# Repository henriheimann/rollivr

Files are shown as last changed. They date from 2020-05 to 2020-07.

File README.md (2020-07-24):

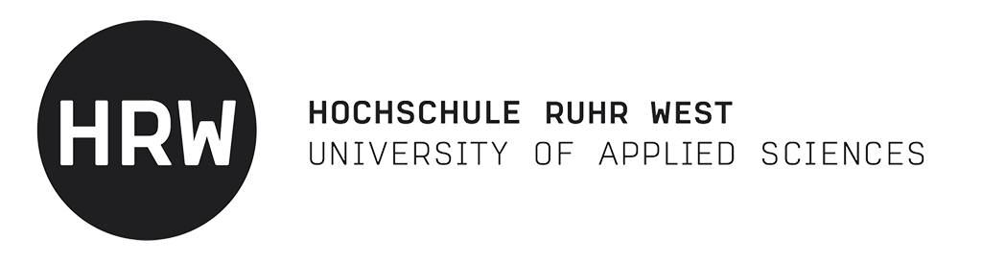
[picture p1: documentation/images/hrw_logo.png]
HRW Logo

<br/>
<br/>
<br/>

# RolliVR

This repository contains the documentation and the software and hardware components of the RolliVR project developed at [Hochschule Ruhr West](https://www.hochschule-ruhr-west.de/). RolliVR aims to create a platform for wheelchair drivers to use their wheelchair to naturally move in existing VR applications and games. For that purpose, we provide a manual along the design files for 3D-prints to create the platform and an OpenVR driver and software package to use the platform in SteamVR applications.





</br>

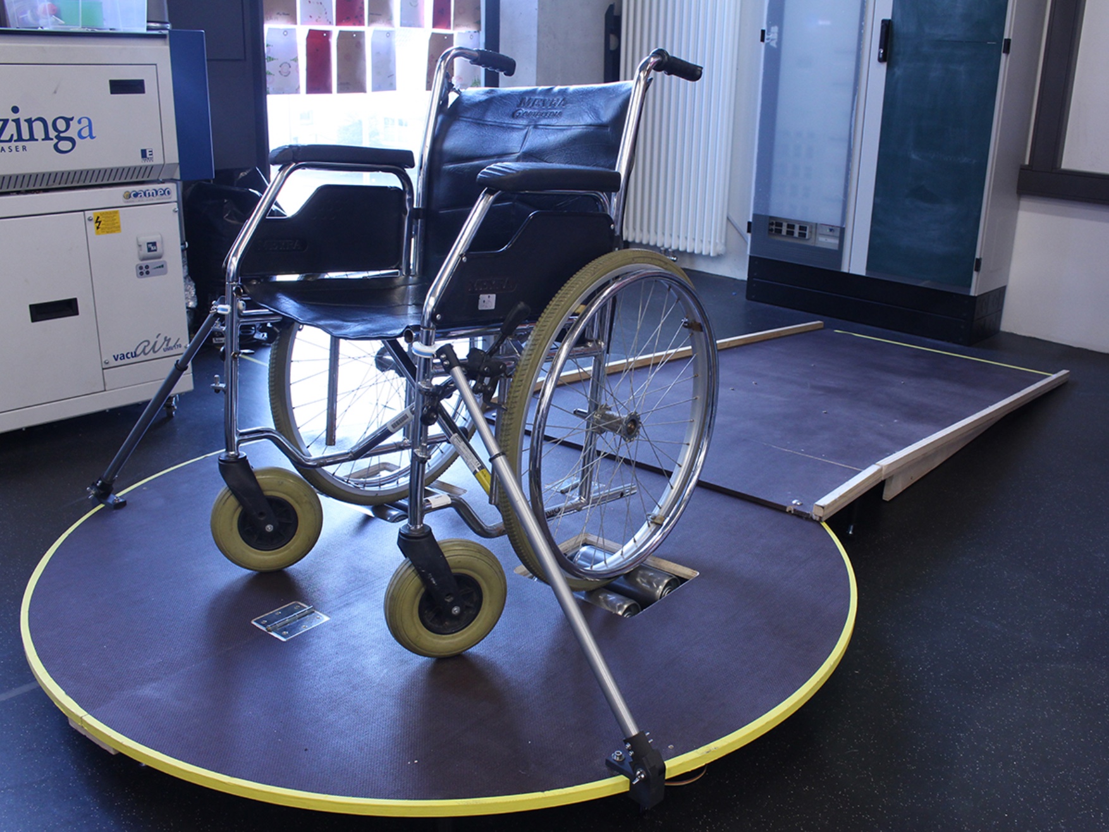
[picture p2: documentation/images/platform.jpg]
Platform


</br>
</br>

## Readme Contents

- [Building the Platform](#building-the-platform)
    - [Bill of Materials](#bill-of-materials)
    - [3D-Printed Components](#3D-Printed-Components)
    - [Electronics](#electronics)
    - [Assembly](#assembly)
- [Building the Software](#building-the-software)
    - [Required Software](#required-software)
    - [Arduino](#arduino)
    - [Driver and Overlay](#driver-and-overlay)
- [Usage Guide](#usage-guide)

## Building the Platform

### Bill of Materials

| Count | Part | Used For |
| - | - | - |
| 1 | Arduino Uno (or similar) | electronics |
| 1 | USB cable for the chosen Arduino | electronics |
| 1 | USB extension cable | electronics |
| 2 | Grove optical rotary encoder (TCUT1600X01) | electronics |
| 2 | Grove universal 4 pin cable | electronics |
| - | jumper wires | electronics |
| 2 | film coated plywood 1500x7500mm (thickness 18mm) | platform |
| 2 | hinges | platform |
| 8 | height adjustable feet (height around 10mm) | platform |
| 2 | load bearing rollers (length 200mm, diameter 80mm, 12mm thread) | platform |
| 8 | stainless steel angle brackets | platform |
| 8+ | M12 nuts | platform |
| 40+ | M5 pointed screws | platform |
| 2 | telescopic tubes (length around 1m, diameter 18mm to 22.5mm) | wheelchair bracket |
| 8+ | M3 screws (length 40mm) | wheelchair bracket |
| 8+ | M3 nuts | wheelchair bracket |
| 8+ | M3 washers | wheelchair bracket |
| 6+ | M5 screws (length 40mm) | wheelchair bracket |
| 6+ | M5 nuts | wheelchair bracket |
| 6+ | M5 washers | wheelchair bracket |
| - | flexible filament (TPU) | wheelchair bracket |
| - | dark filament | encoder disk |
| - | any filament | other 3D-printed parts |
| - | double sided tape | encoder disk |
| - | duct tape | wiring |

### 3D-Printed Components

#### Encoder Ring

The encoder ring must be printed with a dark filament to properly block the light of the rotary encoder's LEDs. ([.stl](hardware/encoder-ring/encoder-ring.stl))

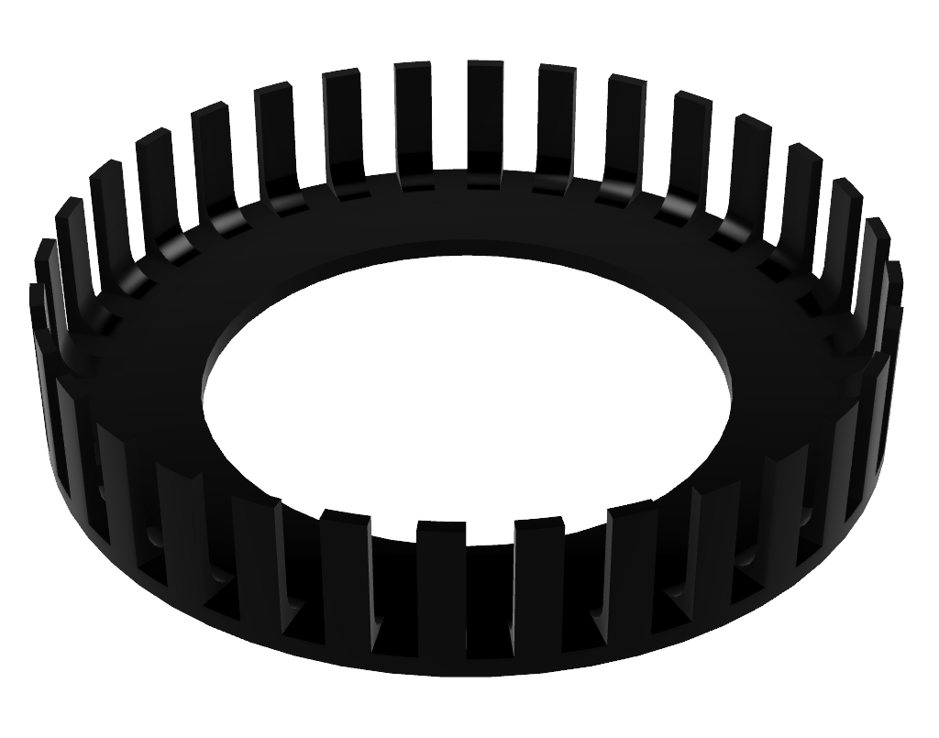
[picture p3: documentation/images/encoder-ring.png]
Encoder Ring


#### Encoder Holder

The encoder holder can be printed with a filament of your choice. ([.stl](hardware/encoder-holder/encoder-holder.stl))

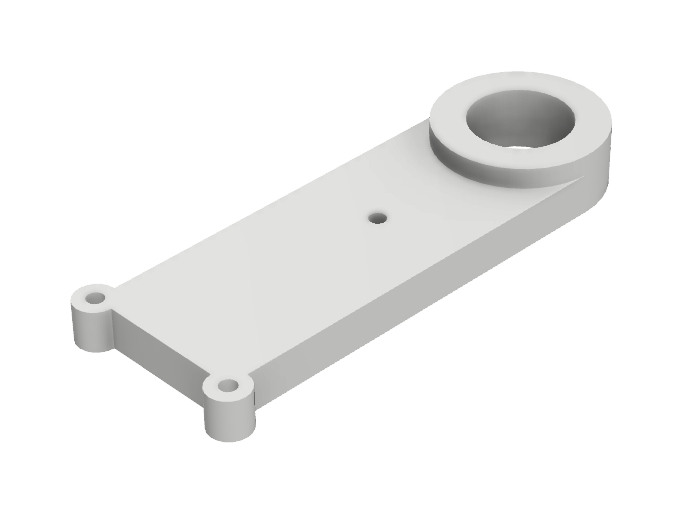
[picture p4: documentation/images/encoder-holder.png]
Encoder Holder


#### Platform Bracket

Both parts of the platform bracket can be printed with a filament of your choice. ([first .stl](hardware/platform-bracket/platform-bracket-1.stl), [second .stl](hardware/platform-bracket/platform-bracket-2.stl))

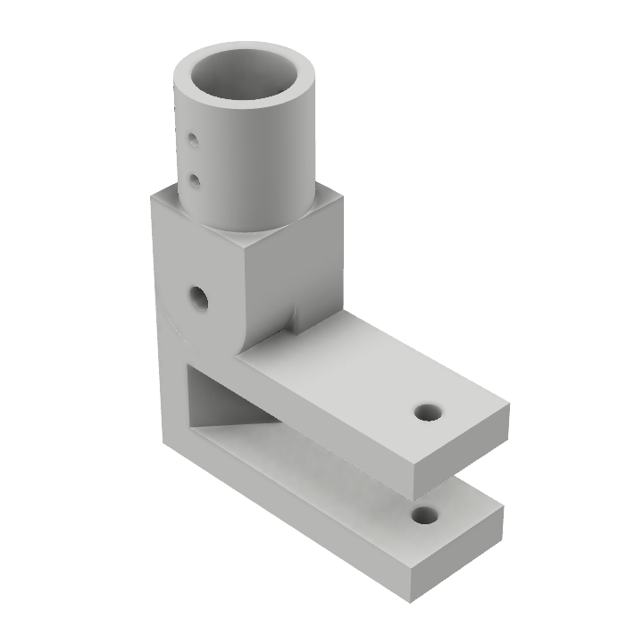
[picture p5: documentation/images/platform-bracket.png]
Platform Bracket


#### Wheelchair Bracket

Most parts of the wheelchair bracket can be printed with a filament of your choice. ([first .stl](hardware/wheelchair-bracket/wheelchair-bracket-1.stl), [second .stl](hardware/wheelchair-bracket/wheelchair-bracket-2.stl)) The part holding onto the wheelchair should be printed with flexible filament (TPU) for a better grip and to prevent any scratches. ([third .stl](hardware/wheelchair-bracket/wheelchair-bracket-3.stl)) The second and third parts (the parts holding onto the wheelchair) have to be printed twice to form the grip.  

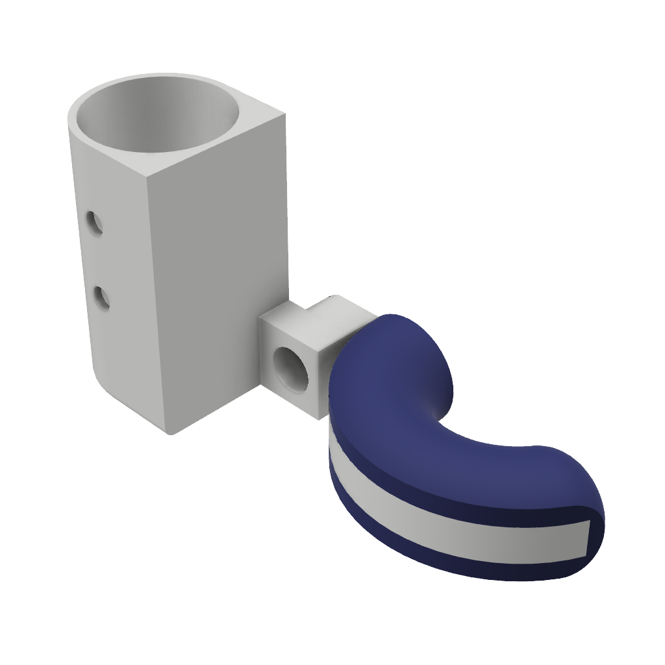
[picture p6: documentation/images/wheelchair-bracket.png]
Wheelchair Bracket
 

### Assembly

#### Platform

Firstly, cut the two film coated plywood boards into semicircles with a diameter of 750mm. Align them and use two hinges to combine the two halves into a complete circle. This allows for easier transport of the platform. Cut out two holes which will later house the load bearing rollers according to the following drawing.

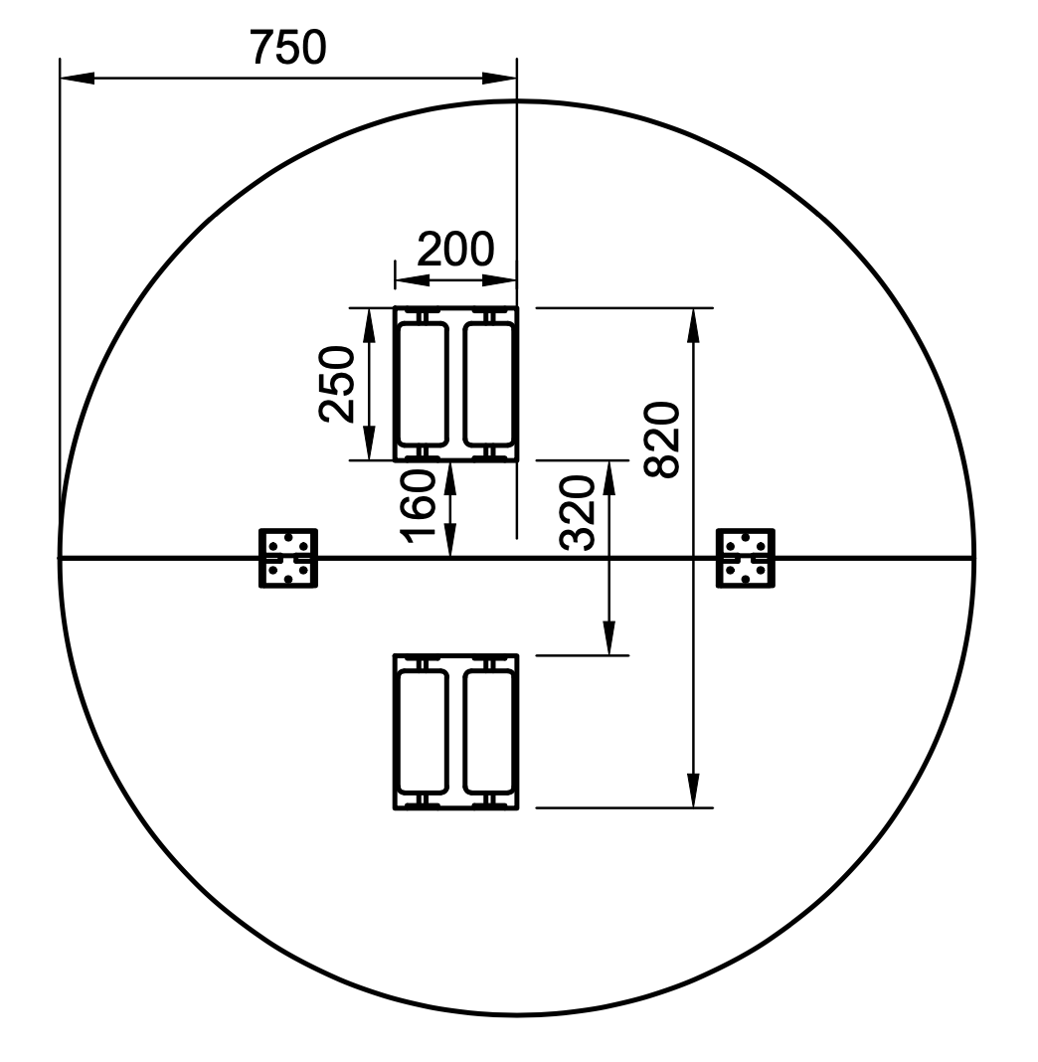
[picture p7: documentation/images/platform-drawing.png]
Platform Drawing


Evenly space out and screw the eight height adjustable feet to the bottom of the board to elevate it to a height of about 10cm.

#### Rollers

Place the 3d-printed encoder rings over two of the rollers and fixate them using double sided tape on their bottom side.

Use a single screw to fix the optical rotary encoder onto the 3d printed holder. Anchor each load bearing roller between two angle brackets putting the rotary encoder holders (where applicable) and nuts in between as seen in the image below.

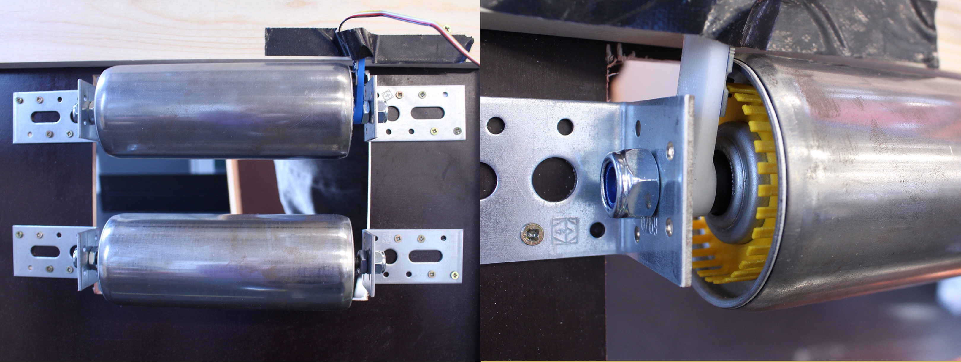
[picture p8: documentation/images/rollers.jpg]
Rollers


Screw the angle brackets to the platform afterwards.

#### Bracket

Assemble the wheelchair and platform brackets using the M5 and M3 screws, nuts and washers as seen in the image below.

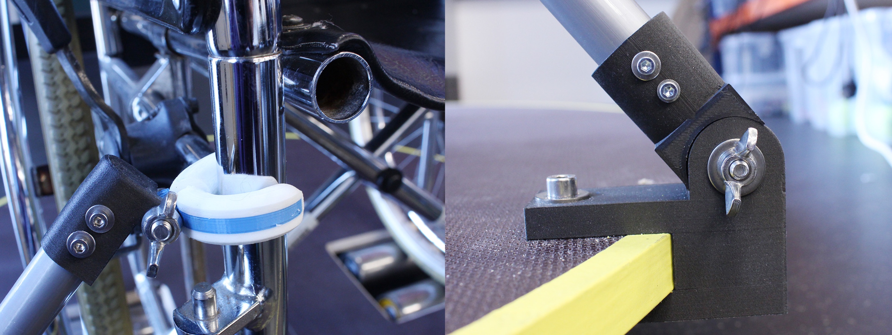
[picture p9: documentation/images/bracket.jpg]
Bracket


### Electronics

Both optical encoders need to be connected to the Arduino's VCC and ground pins and the respective digital input pins 6 to 9 as shown in the image below.

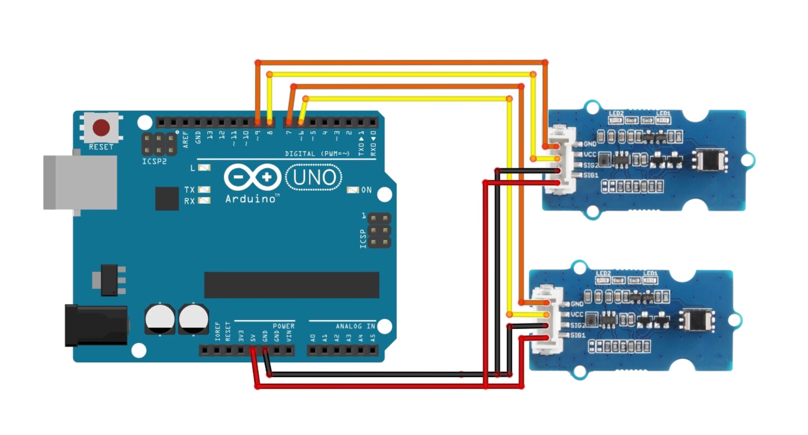
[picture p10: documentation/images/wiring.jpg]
Wiring


## Building the Software

### Required Libraries & Tools

| Software | License | Recommended Installation Method |
| - | - | - |
| Qt5 | LGPLv3 | Download and install from [here](https://www.qt.io/download-qt-installer) |
| OpenVR | BSD 3 | Install via vcpkg |
| GLM | MIT | Install via vcpkg |
| Serial | MIT | Fork integrated as submodule of this repository |
| NSIS | zlib | Download install from [here](https://nsis.sourceforge.io/Download) |
| NSIS Json Plugin | See LICENSE.txt | Included in this repository |
| CMake | New BSD | Download and install from [here](https://cmake.org/download/) |
| Arduino IDE | LGPL | Download and install from [here](https://www.arduino.cc/en/main/software) |

### Driver and Overlay

[CMake](https://cmake.org/download/) is used as build tool. OpenVR and GLM libraries need to be installed on your machine. It is recommended that you download them via [vcpkg](https://github.com/Microsoft/vcpkg). Make sure to install the x64-windows triplets to be able to build the driver and overlay as 64 bit applications:

`vcpkg install openvr glm --triplet x64-windows`

[Qt5](https://www.qt.io/download-open-source) has to be installed to build the overlay, as it is used for the user interface. To build the installer [NSIS](https://nsis.sourceforge.io/Download) has to be installed. With this prerequisites installed and the repository cloned, make sure that you that you have initialized the required submodules via the execution of the following command in the root directory:

`git submodule update --init`

In the software directory, create a build directory and move to it:

`cd software && mkdir build && cd build`

Execute CMake, make sure the TOOLCHAIN_FILE and PREFIX_PATH variables match your installation paths. Set your required release type and specify the generator:

`cmake .. -DCMAKE_BUILD_TYPE=Release -G"Visual Studio 16 2019" -DCMAKE_TOOLCHAIN_FILE=C:\vcpkg\scripts\buildsystems\vcpkg.cmake -DCMAKE_PREFIX_PATH=C:\Qt\5.14.2\msvc2017_64\lib\cmake`

Perform the build:

`cmake --build . --config Release`

After the build, the driver folder structure and files will available as `<Path to Repo>\software\build\driver\rollivr` and the overlay folder structure and files will be copied to the output folder as `<Path to Repo>\software\build\overlay\rollivr`.

If you want to create the installer execute the following command:

`cmake --build . --target package --config Release`

The installer will then be located at `<Path to Repo>\build\RolliVR-Installer.exe`.
	
Alternatively, you can access the most recent prebuild installer in the latest completed action.

### Arduino

There are two Arduino projects provided in this repository:

- [arduino-software-debug](embedded/arduino-software-debug) serves as a mean to test the software without the platform. Simply wire two pushbuttons with pullup resistors to the A0 and A5 pins of an Arduino and flash this sketch. Holding down buttons simulates a forward movement of the left and right wheels.

- [arduino-software-encoder](embedded/arduino-software-encoder) is the software required for the real platform. It transmits the movement distance and angle calculated from the values of the optical rotary encoders every 100 milliseconds. It also applies a rolling average filter over 5 samples.

## Usage Guide

After building `RolliVR-Installer.exe` launch it and install RolliVR to a directory of your choice.

### Driver

Launch SteamVR after the installation. Connect the Arduino with the firmware flashed to the PC running SteamVR and take a look at the information panel. If no icon is shown at all, make sure an entry in the `external_drivers` array in the `<User>\AppData\Local\openvr\openvrpaths.vrpath` file points to `<RolliVR Installation Directory>\driver\rollivr`. If the RolliVR icon is greyed out, the connection could not be established, if it is blue-greenish, the Arduino is successfully sending data.

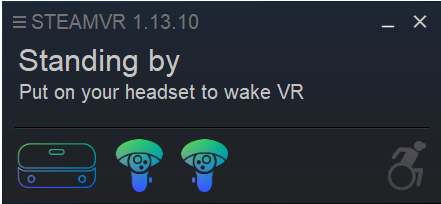
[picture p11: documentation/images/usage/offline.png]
Offline

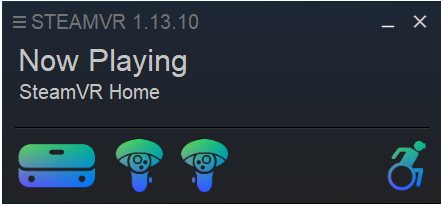
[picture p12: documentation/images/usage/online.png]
Online


In case of a failed connection go to the SteamVR developer console:

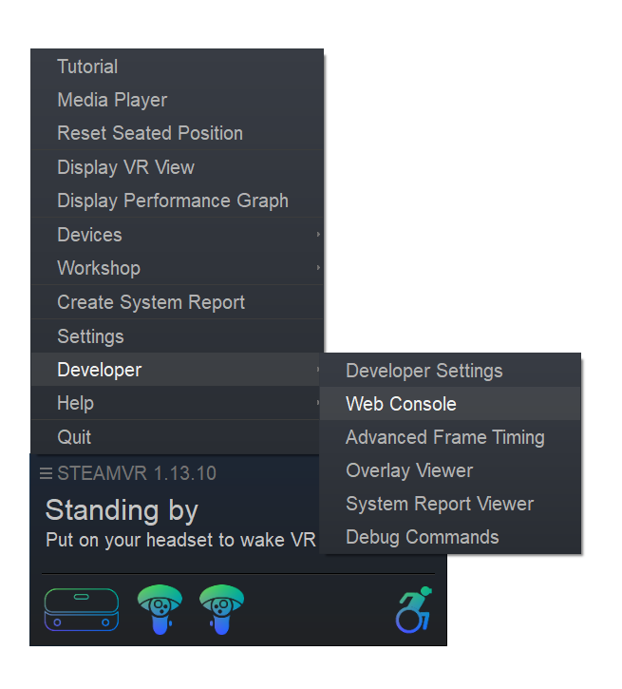
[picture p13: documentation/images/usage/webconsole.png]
Web Console


Search for RolliVR and find the logs of available and accepted hardware ids. Available hardware ids are the ids of serial ports connected to your system. Accepted hardware ids are the ids the driver expects.

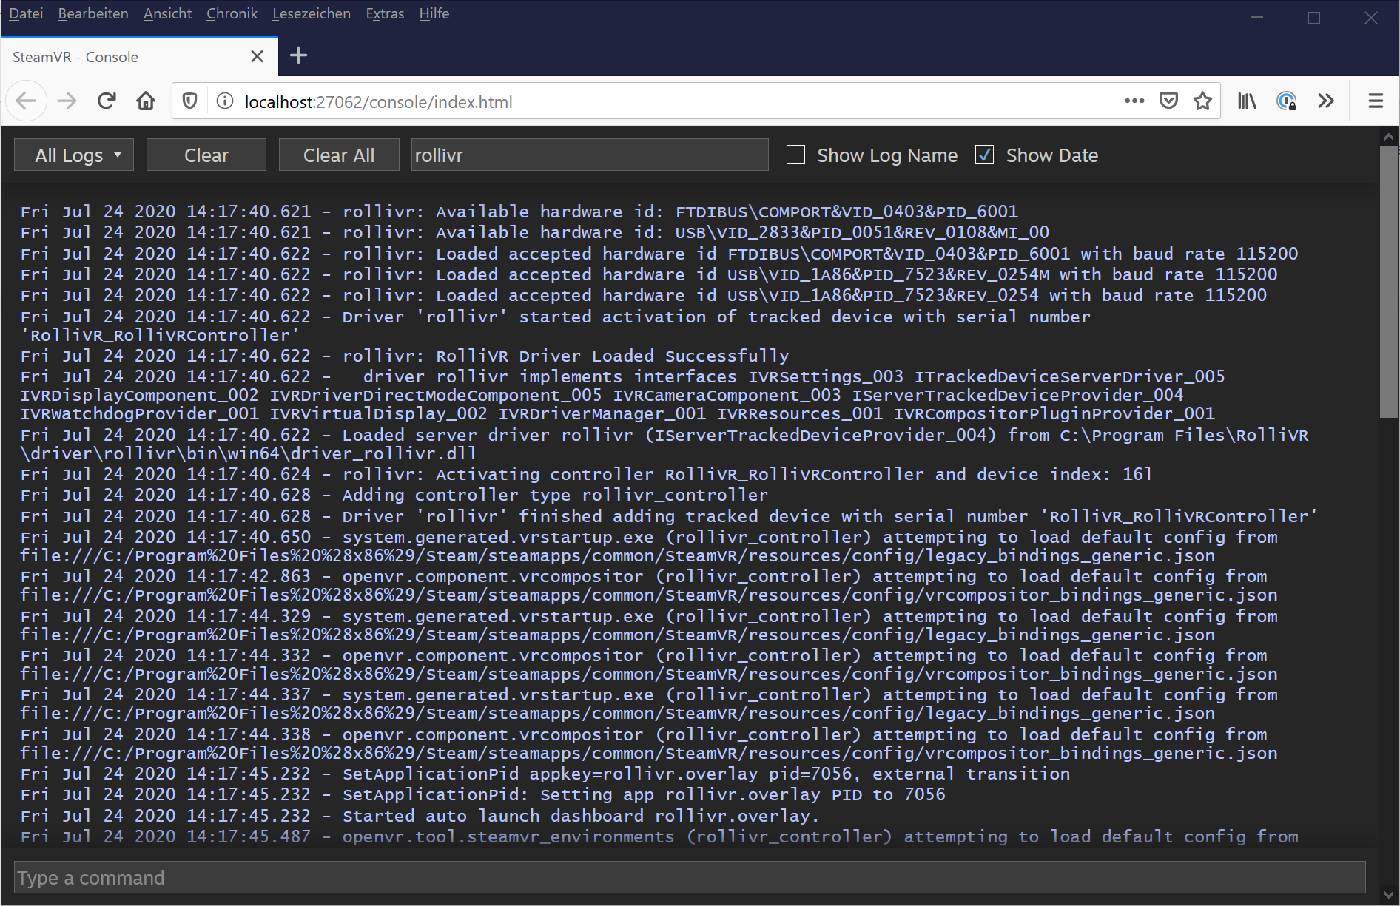
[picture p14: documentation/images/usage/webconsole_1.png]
Web Console


If your Arduino has a hardware id that is not accepted, add the hardware id and baudrate to the config file located at `<RolliVR Installation Directory>\driver\rollivr\resources\config\comports.txt`. Restart SteamVR afterwards. The Arduino should successfully connect and you can test the controller by accessing `#/USER/TREADMILL` under Controllers > Test Controller. VR Applications that allow custom controller bindings can now be configured to use the RolliVR controller as an input.

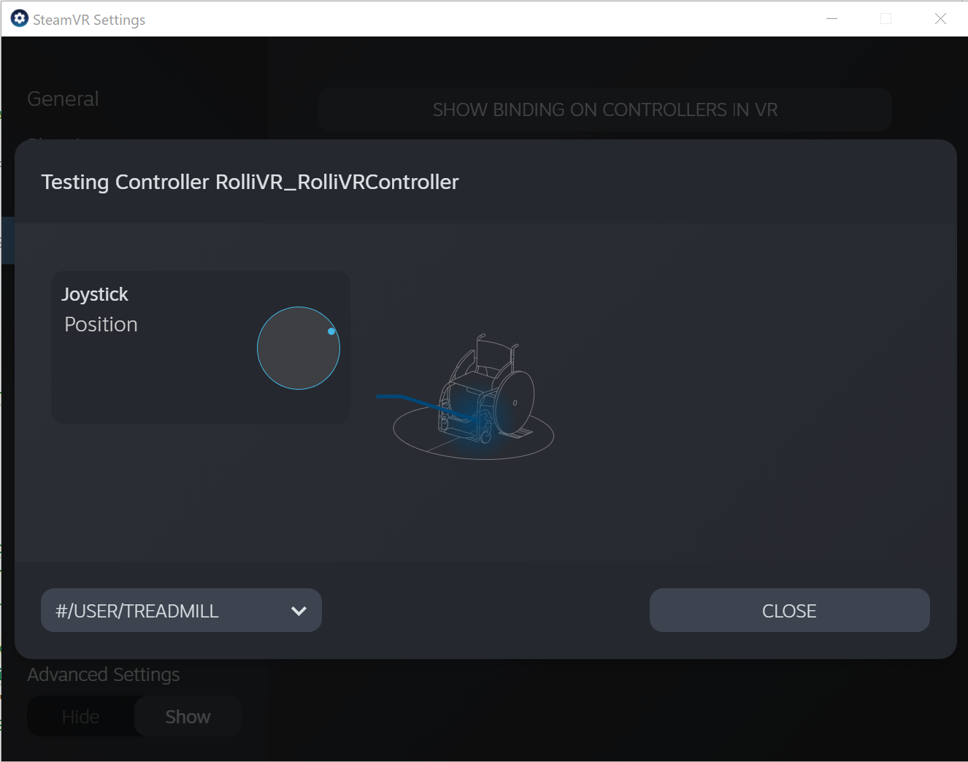
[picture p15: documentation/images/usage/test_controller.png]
Test Controller


### Overlay

When using roomscale VR applications with RolliVR, the overlay is required. To make sure the overlay has correctly registered itself as an autostart application, go to Choose Startup Overlay Apps under Startup / Shutdown. If RolliVR is displayed, you are good to continue, otherwise run `install_manifest.bat` in the installation directory and restart SteamVR. RolliVR should now be correctly registered and enabled as autostart application:

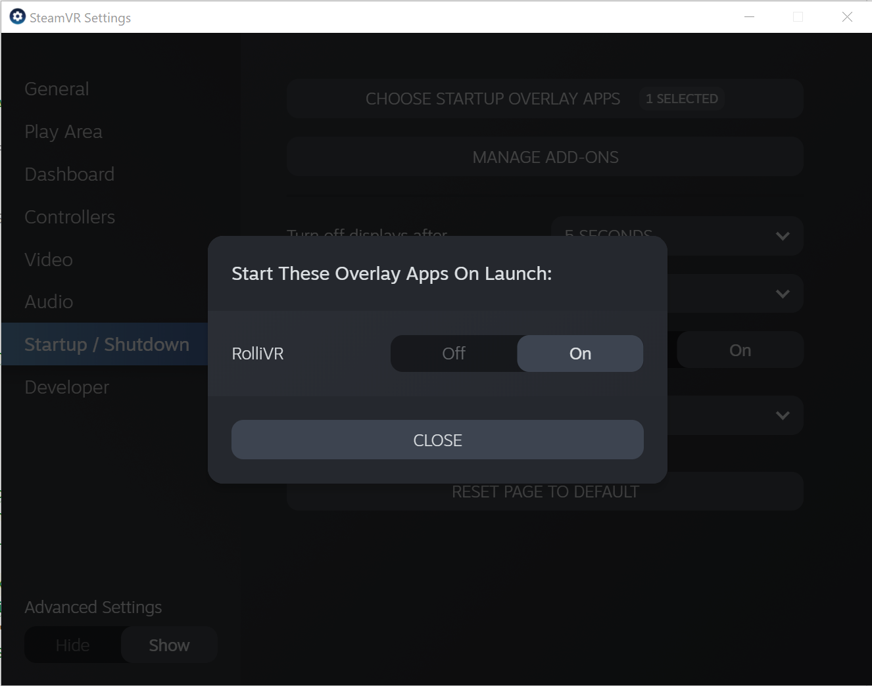
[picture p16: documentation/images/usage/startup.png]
Autostart Applications


The driver and the overlay need to be connected next. Go to the Controllers and make sure advanced settings are shown. Click on Show Old Binding UI.

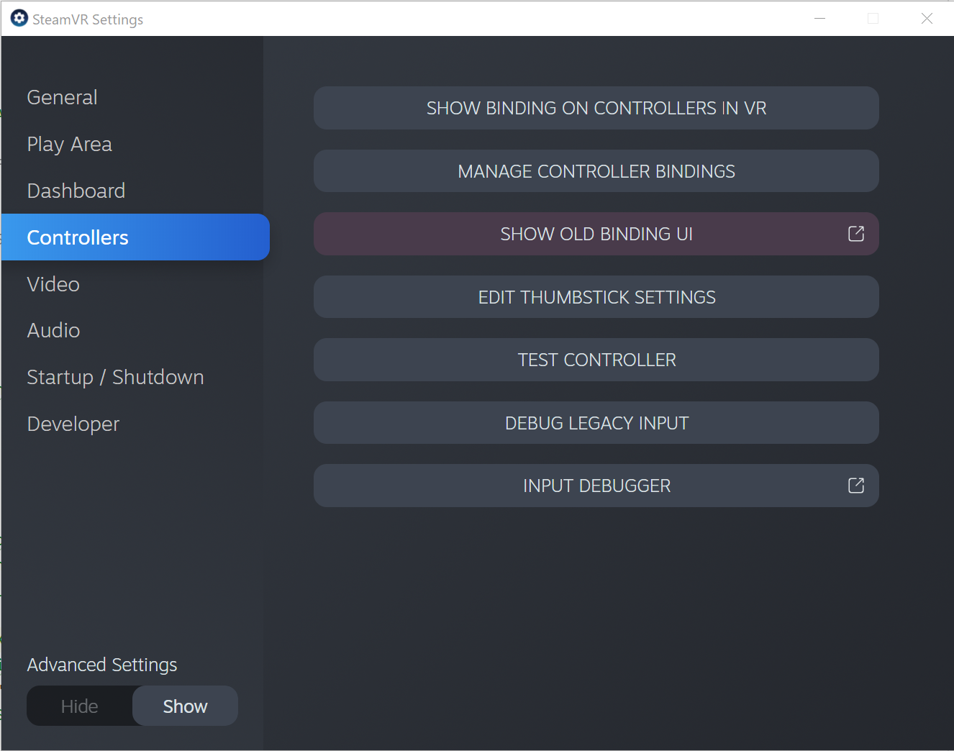
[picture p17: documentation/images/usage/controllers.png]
Controllers Menu


Now proceed to edit the bindings of RolliVR. You may need to click on Show More Applications before it shows up.

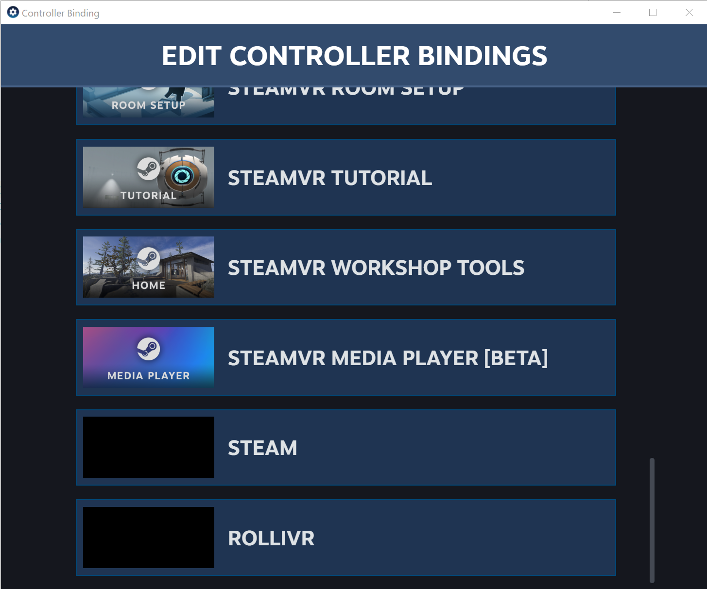
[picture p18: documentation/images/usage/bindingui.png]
Binding UI


Firstly, change the controller used for the RolliVR application. This defaults to your VR headsets controllers, but it needs to be changed to the RolliVR Controllers. To do so, click on the name of the Current Controller and select the RolliVR Controller in the following menu.

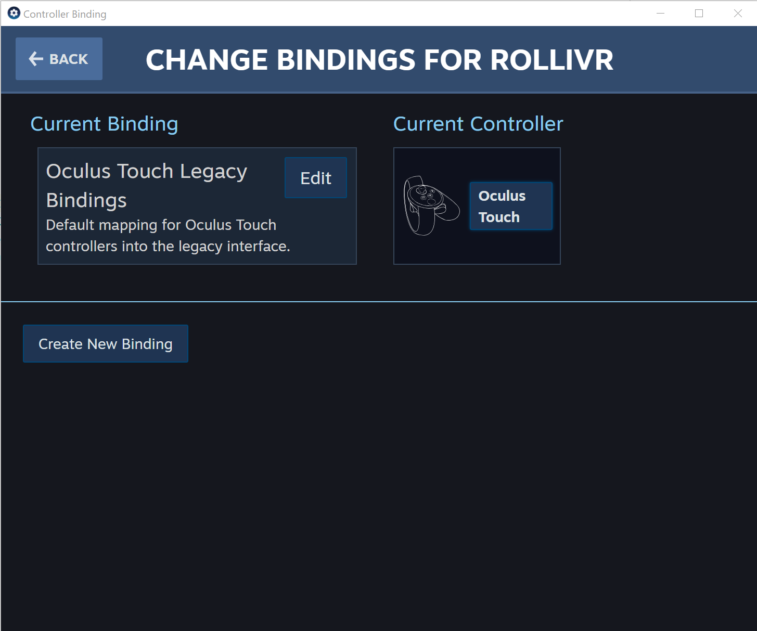
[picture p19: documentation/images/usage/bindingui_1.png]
Binding UI


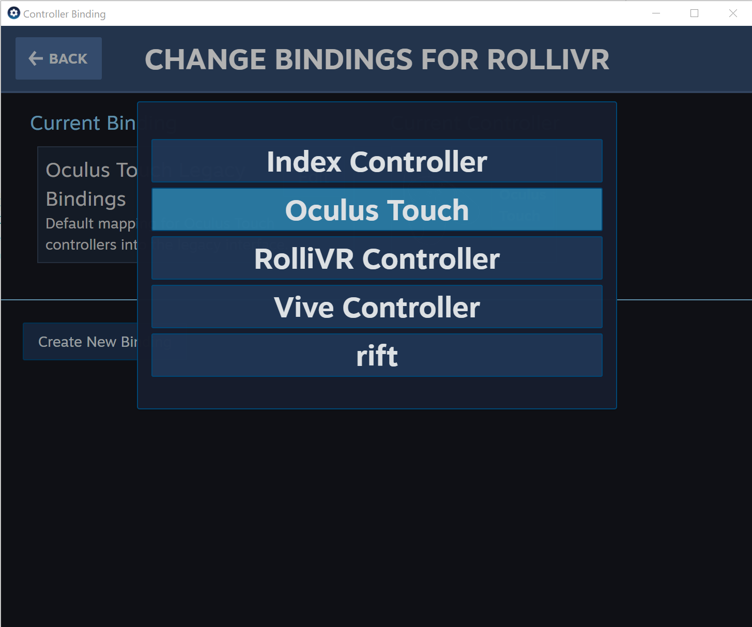
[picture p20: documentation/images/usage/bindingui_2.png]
Binding UI


Secondly, activate the default RolliVR Overlay bindings for the RolliVR controller under Official Bindings.

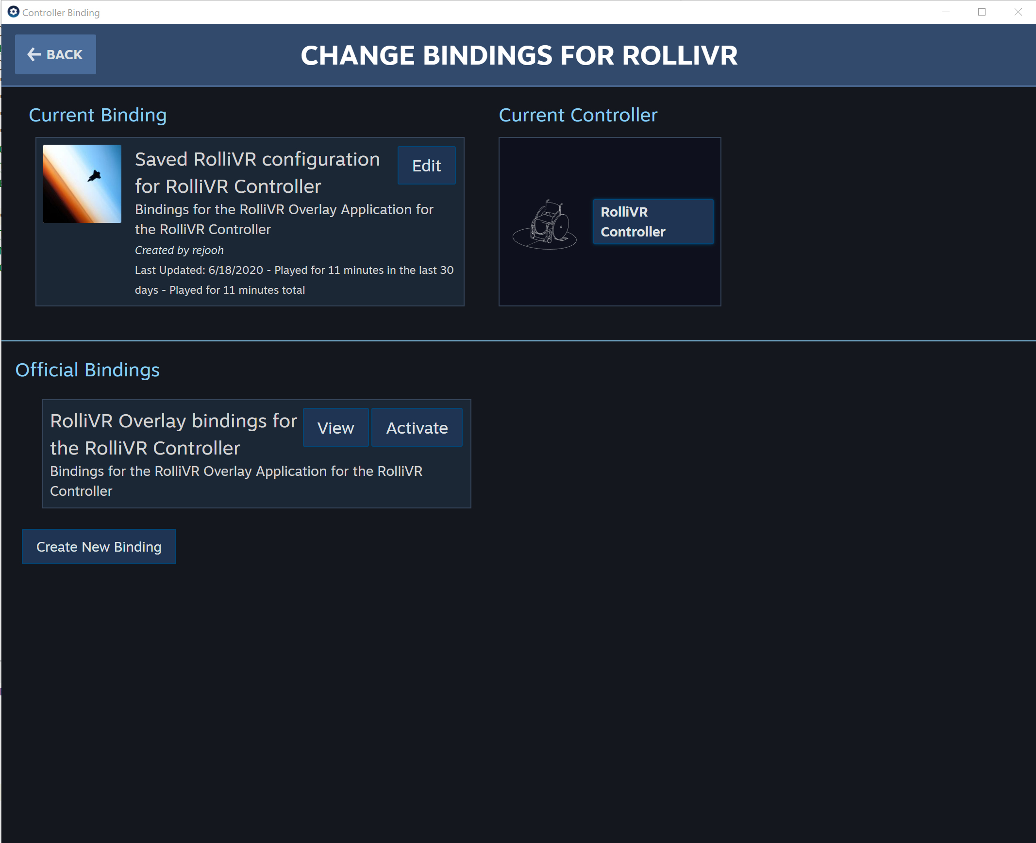
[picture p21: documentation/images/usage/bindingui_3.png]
Binding UI


With that step done, the overlay is fully functional and you can access it in VR using the SteamVR menu. The RolliVR icons appears on the lower left corner.

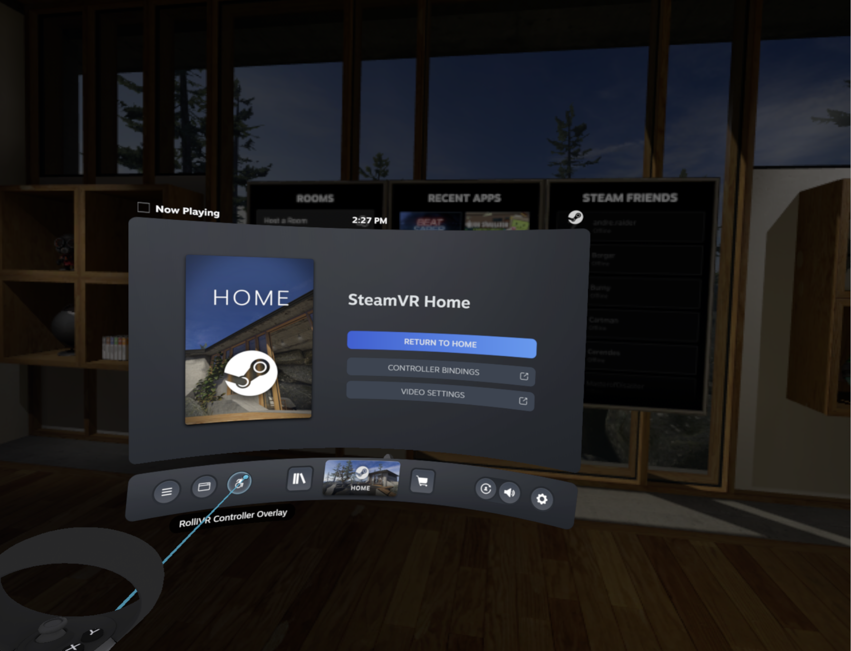
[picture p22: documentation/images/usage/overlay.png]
Overlay


To start moving in roomscale VR applications, push the Start Forced Movement button while seated on the platform and looking straight ahead. The menu must be closed for the movement to work.

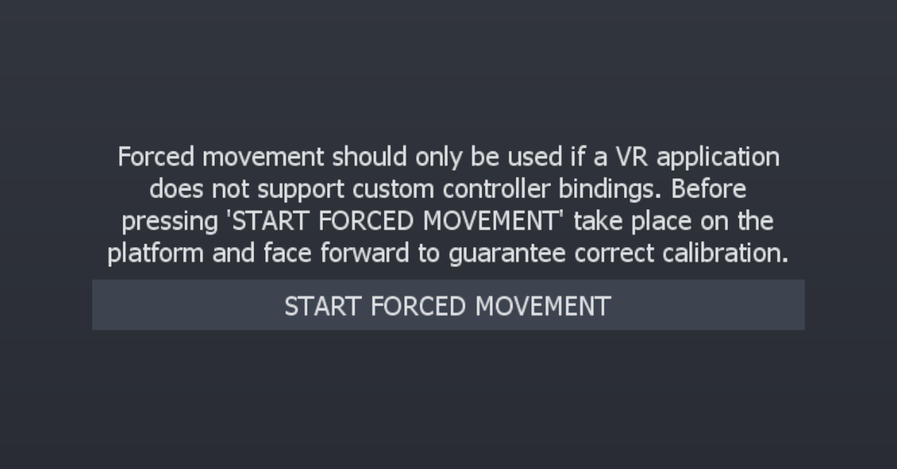
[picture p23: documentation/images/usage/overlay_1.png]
Overlay


Inputs to the wheelchair now move you around the room. To reset your movement and return to the origin, push Reset Accumulated Movement. To stop the movement with the wheelchair, push Stop Forced Movement. Turn and Movement Speeds as well as a height offset can be configured in this menu, too.

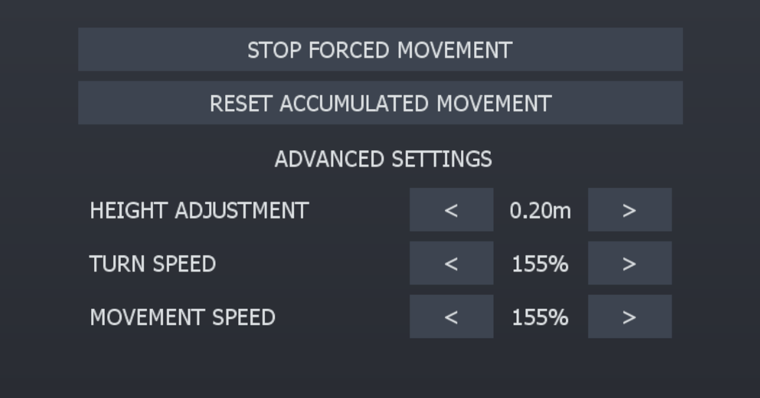
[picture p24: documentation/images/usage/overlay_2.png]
Overlay


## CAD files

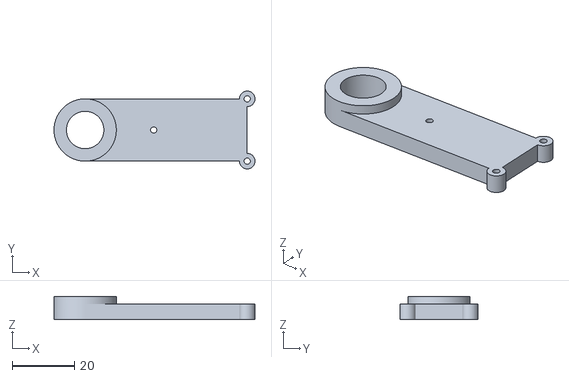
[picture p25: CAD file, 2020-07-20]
hardware/encoder-holder/encoder-holder.stl
64.5 x 25.0 x 7.50

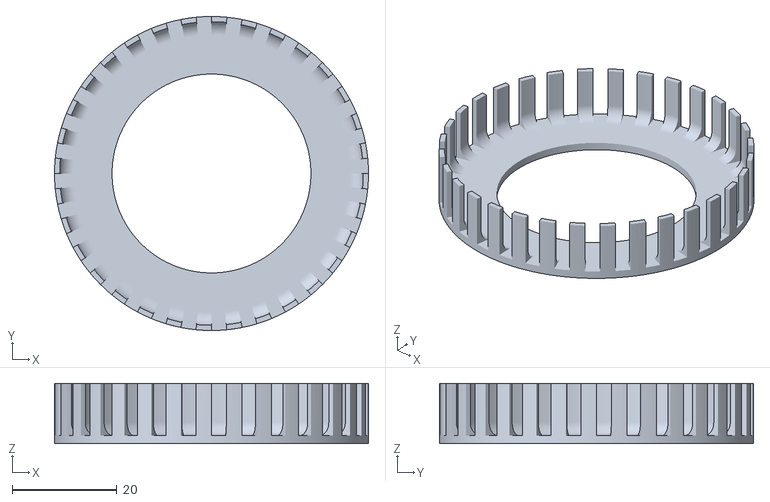
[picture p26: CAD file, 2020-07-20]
hardware/encoder-ring/encoder-ring.stl
60.0 x 60.0 x 11.5

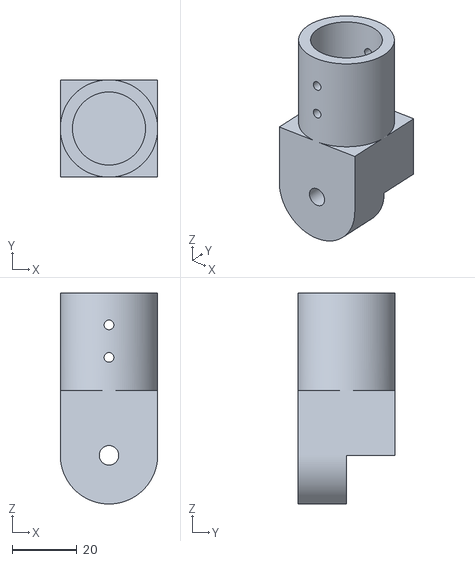
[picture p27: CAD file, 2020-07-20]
hardware/platform-bracket/platform-bracket-1.stl
30.0 x 30.0 x 65.0

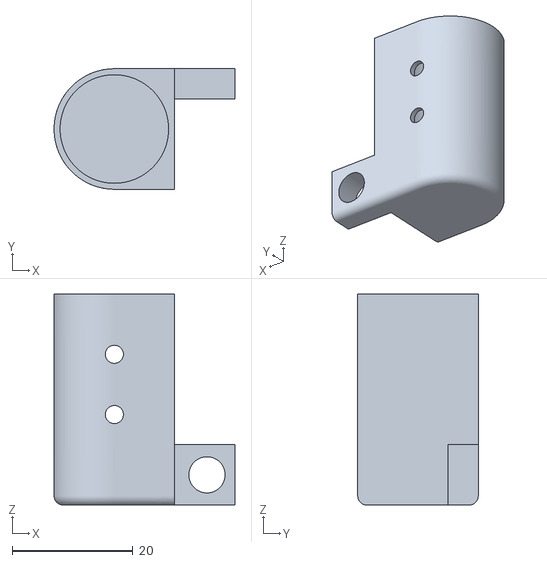
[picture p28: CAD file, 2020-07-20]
hardware/wheelchair-bracket/wheelchair-bracket-1.stl
30.0 x 20.0 x 35.0

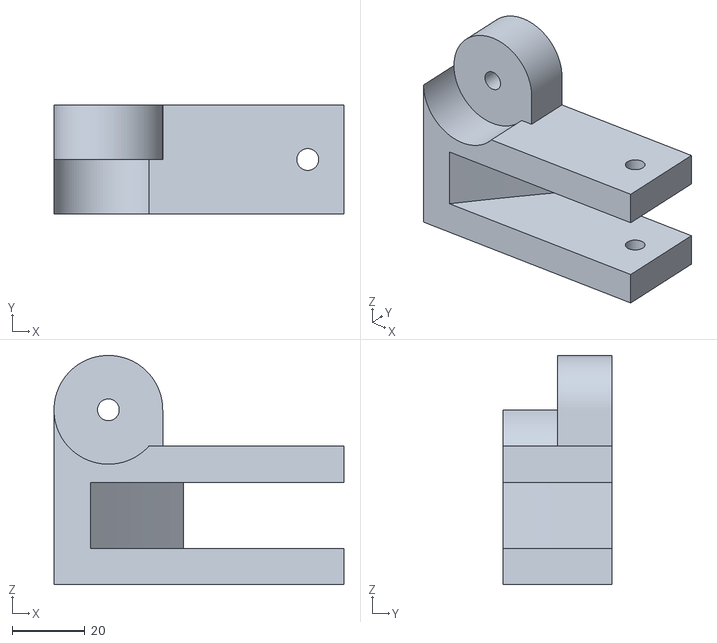
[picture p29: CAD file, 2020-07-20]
hardware/platform-bracket/platform-bracket-2.stl
80.0 x 30.0 x 63.2

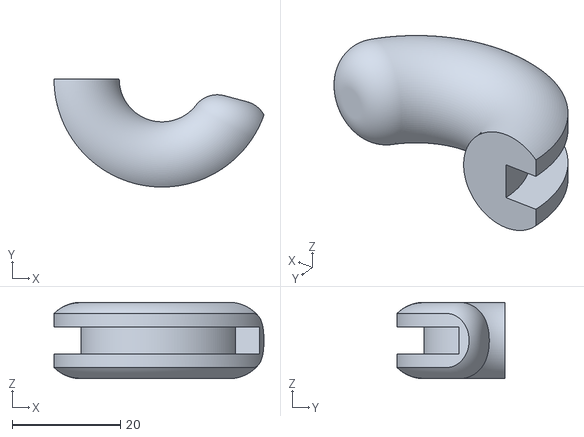
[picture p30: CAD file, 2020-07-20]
hardware/wheelchair-bracket/wheelchair-bracket-3.stl
38.9 x 20.0 x 14.1

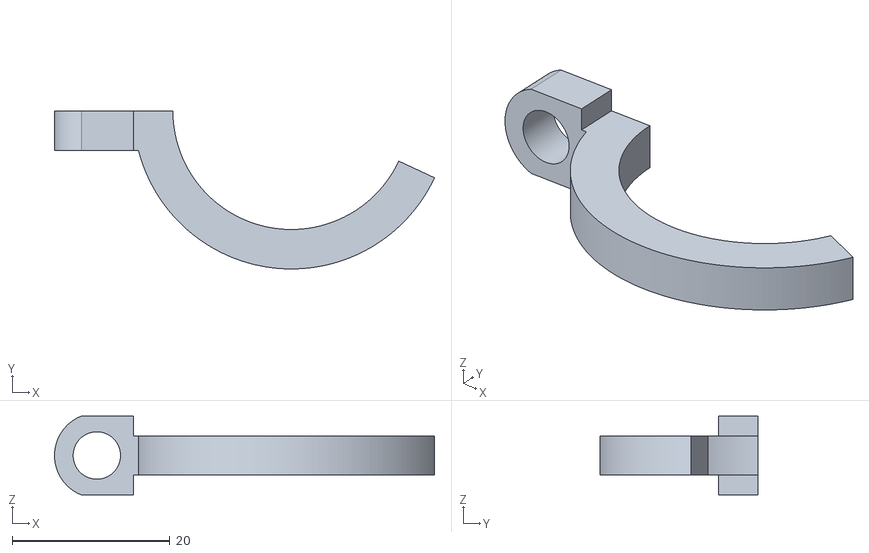
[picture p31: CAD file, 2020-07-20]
hardware/wheelchair-bracket/wheelchair-bracket-2.stl
48.1 x 20.0 x 10.0

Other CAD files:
hardware/encoder-holder/encoder-holder.f3d
hardware/encoder-ring/encoder-ring.f3d
hardware/platform-bracket/platform-bracket.f3d
hardware/wheelchair-bracket/wheelchair-bracket.f3d

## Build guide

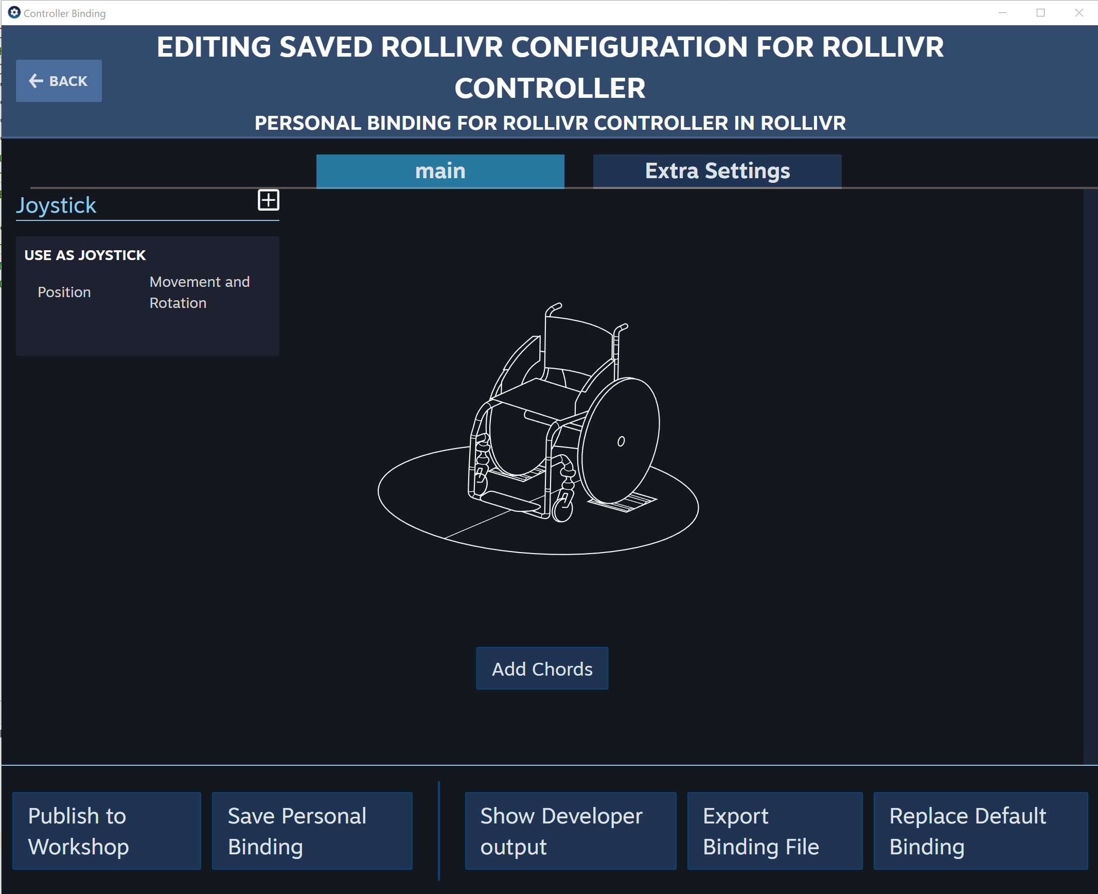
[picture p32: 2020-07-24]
documentation/images/usage/bindingui_4.png

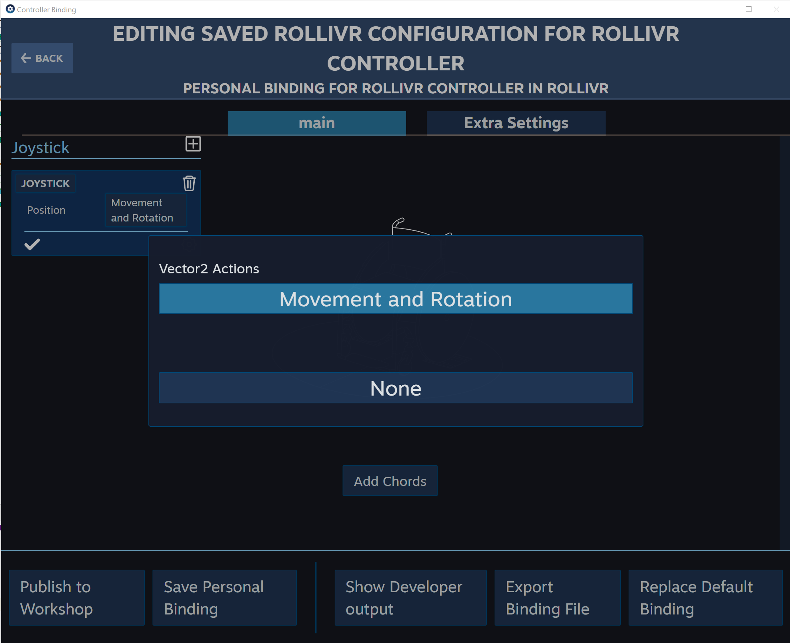
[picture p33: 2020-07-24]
documentation/images/usage/bindingui_5.png

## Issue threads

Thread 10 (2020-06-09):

Add a standby modus icon for the driver

henriheimann, 2020-06-09:
SteamVR shows the driver as standby after some time because it is not moving. This icon has to be created and added.

henriheimann, 2020-06-21:
Was fixed by b2bae2790ffe58a409ddb76cbab27b2bed32b787 which added modern SteamVR icons.

Closed 2020-06-21.

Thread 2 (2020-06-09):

The overlay application should start automatically with SteamVR

henriheimann, 2020-06-09:
To start automatically, the overlay application has to register itself with a manifest. See pending issue: https://github.com/ValveSoftware/openvr/issues/1378

Closed 2020-06-16.

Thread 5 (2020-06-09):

Reset Movement when starting a new application through SteamVR

henriheimann, 2020-06-09:
When starting a new application through SteamVR the current movement and rotation offsets should be reset to not confuse the user, because he otherwise doesn't start at the normal starting position.

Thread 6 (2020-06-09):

Add an easy translation and rotation reset button in the overlay

henriheimann, 2020-06-09:
Reset of translation and rotation is something the user of the overlay frequently requires.

Closed 2020-06-18.

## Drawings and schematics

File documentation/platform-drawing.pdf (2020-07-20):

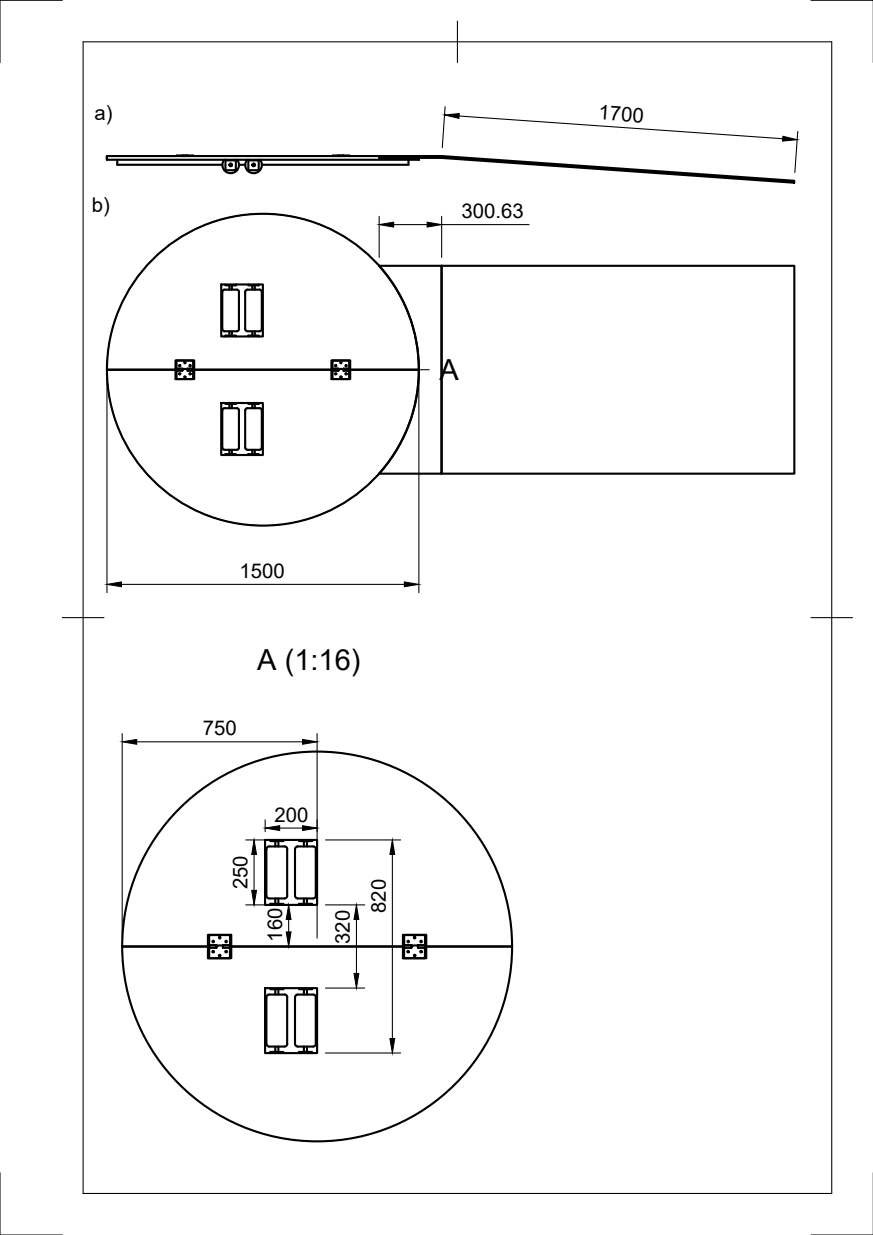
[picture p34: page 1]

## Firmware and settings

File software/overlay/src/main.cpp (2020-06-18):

#include "main.h"
#include "RolliVROverlayWidget.h"
#include "RolliVROverlayController.h"

#include <QtWidgets/QApplication>
#include <iostream>

void RolliVROverlay::installManifest(bool cleanInstall)
{
	// Adapted code from: https://github.com/matzman666/OpenVR-AdvancedSettings/

	auto manifestQPath = QDir::cleanPath(QDir(QCoreApplication::applicationDirPath()).absoluteFilePath("manifest.vrmanifest"));
	if (QFile::exists(manifestQPath)) {
		bool alreadyInstalled = false;
		if (vr::VRApplications()->IsApplicationInstalled(RolliVROverlay::applicationKey)) {
			if (cleanInstall) {
				char buffer[1024];
				auto appError = vr::VRApplicationError_None;
				vr::VRApplications()->GetApplicationPropertyString(RolliVROverlay::applicationKey, vr::VRApplicationProperty_WorkingDirectory_String, buffer, sizeof(buffer), &appError);
				if (appError == vr::VRApplicationError_None) {
					auto oldManifestQPath = QDir::cleanPath(QDir(buffer).absoluteFilePath("manifest.vrmanifest"));
					if (oldManifestQPath.compare(manifestQPath, Qt::CaseInsensitive) != 0) {
						vr::VRApplications()->RemoveApplicationManifest(QDir::toNativeSeparators(oldManifestQPath).toStdString().c_str());
					} else {
						alreadyInstalled = true;
					}
				}
			} else {
				alreadyInstalled = true;
			}
		}
		auto appError = vr::VRApplications()->AddApplicationManifest(QDir::toNativeSeparators(manifestQPath).toStdString().c_str());
		if (appError != vr::VRApplicationError_None) {
			throw std::runtime_error(std::string("Could not add application manifest: ") + std::string(vr::VRApplications()->GetApplicationsErrorNameFromEnum(appError)));
		} else if (!alreadyInstalled || cleanInstall) {
			appError = vr::VRApplications()->SetApplicationAutoLaunch(RolliVROverlay::applicationKey, true);
			if (appError != vr::VRApplicationError_None) {
				throw std::runtime_error(std::string("Could not set auto start: ") + std::string(vr::VRApplications()->GetApplicationsErrorNameFromEnum(appError)));
			}
		}
	} else {
		throw std::runtime_error(std::string("Could not find application manifest: ") + manifestQPath.toStdString());
	}
}

void RolliVROverlay::removeManifest()
{
	// Adapted code from: https://github.com/matzman666/OpenVR-AdvancedSettings/

	auto manifestQPath = QDir::cleanPath(QDir(QCoreApplication::applicationDirPath()).absoluteFilePath("manifest.vrmanifest"));
	if (QFile::exists(manifestQPath)) {
		if (vr::VRApplications()->IsApplicationInstalled(RolliVROverlay::applicationKey)) {
			vr::VRApplications()->RemoveApplicationManifest(QDir::toNativeSeparators(manifestQPath).toStdString().c_str());
		}
	} else {
		throw std::runtime_error(std::string("Could not find application manifest: ") + manifestQPath.toStdString());
	}
}

void RolliVROverlay::checkForCommandLineArguments(int argc, char *argv[])
{
	if (argc > 1) {
		QCoreApplication coreApp(argc, argv);

		auto exitCode = EXIT_SUCCESS;
		auto initError = vr::VRInitError_None;
		vr::VR_Init(&initError, vr::VRApplication_Utility);

		if (initError != vr::VRInitError_None) {
			std::cerr << "Failed to initialize OpenVR: " << std::string(vr::VR_GetVRInitErrorAsEnglishDescription(initError)) << std::endl;
			exit(EXIT_FAILURE);
		}

		if (std::string(argv[1]) == "-installmanifest") {
			try {
				RolliVROverlay::installManifest(true);
			} catch (std::exception& e) {
				exitCode = EXIT_FAILURE;
				std::cerr << "Failed to install Manifest: " << e.what() << std::endl;
			}
		} else if (std::string(argv[1]) == "-removemanifest") {
			try {
				RolliVROverlay::removeManifest();
			} catch (std::exception& e) {
				exitCode = EXIT_FAILURE;
				std::cerr << "Failed to remove Manifest: " << e.what() << std::endl;
			}
		} else {
			exitCode = EXIT_FAILURE;
			std::cerr << "Unknown argument: " << argv[1] << std::endl;
		}

		vr::VR_Shutdown();
		exit(exitCode);
	}
}

int main(int argc, char *argv[])
{
	RolliVROverlay::checkForCommandLineArguments(argc, argv);

    QApplication application(argc, argv);

    auto *overlayWidget = new RolliVROverlayWidget;
    RolliVROverlayController::SharedInstance()->Init();
    RolliVROverlayController::SharedInstance()->SetWidget(overlayWidget);
    return QApplication::exec();
}

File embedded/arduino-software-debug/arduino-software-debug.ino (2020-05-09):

const int PIN_BUTTON_LEFT = A0;
const int PIN_BUTTON_RIGHT = A5;
const int PIN_LED = LED_BUILTIN;

const float RADIUS = 1.0f;
const float SPEED = 0.8f;

void setup()
{
  pinMode(PIN_BUTTON_LEFT, INPUT);
  pinMode(PIN_BUTTON_RIGHT, INPUT);
  pinMode(PIN_LED, OUTPUT);

  Serial.begin(115200);
}

void loop()
{
 int buttonLeftState = !digitalRead(PIN_BUTTON_LEFT);
 int buttonRightState = !digitalRead(PIN_BUTTON_RIGHT);

 if (buttonLeftState == 1 || buttonRightState == 1) {
   digitalWrite(PIN_LED, HIGH);
 } else {
   digitalWrite(PIN_LED, LOW);
 }

 float distanceLeft = (buttonLeftState == 1) ? SPEED : 0.0f;
 float distanceRight = (buttonRightState == 1) ? SPEED : 0.0f;

 float distance = (distanceLeft + distanceRight) / 2.0f;
 float angle = (distanceLeft - distanceRight) / RADIUS;

 Serial.print(distance);
 Serial.print(",");
 Serial.println(angle);

 delay(10);
}

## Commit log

2020-04-20 Initial commit with example project taken from https://github.com/terminal29/Simple-OpenVR-Driver-Tutorial.git
    [example_controller.obj]
2020-04-21 Remove unneeded project files and rename from example to wheelchair driver
    [wheelchair_controller.obj]
2020-04-22 Add fix version of serial library for now, restructure project and add arduino code
    [wheelchair_controller.obj]
2020-04-22 Add arduino test code
2020-04-28 Restructure project for addition of overlay
    [wheelchair_controller.obj]
2020-04-30 Move source code in src folders of subprojcets
    [wheelchair_controller.obj]
2020-05-03 Add bindingui, mark controller as NeverTracked
    [wheelchair_controller.obj]
2020-05-08 Add drawing of wheelchair platform
2020-05-14 Update UI, add offsets for wheelchair position
2020-05-15 Zero pose (auto) configuration for wheelchair placement in room
2020-05-23 Switch to png thumb icon
2020-05-29 Package and archive driver and overlay
2020-05-29 Add second comport, remove vcpkg caching, fix driver resources copy directory
2020-06-06 Cleanup and comment driver code
2020-06-09 List available and accepted serial ports when starting driver
2020-06-13 Add and remove driver entry in openvrpaths.vrpath during (un-) installation
2020-06-16 Add application manifest and autostart overlay, add modern SteamVR icons
    Fixed #2 by adding an application manifest and autostarting the overlay, also adds modern SteamVR icons for the driver because they seem to not be generated by SteamVR when the driver resides under Program Files.
    [main.cpp]
2020-06-16 Revert to main naming, try to add Qt5 path for CMake
    [main.cpp]
2020-06-18 Add a button to reset the accumulated movement (fixes #6)
    Also removes unnecessary advanced settings and reimplements copying of the application files to the output directory for running the application directly from the build directory without prior installation.
2020-06-21 Implement variable frame timing to fix #4
2020-07-15 Add rolling average filter to arduino software and increase baud rate
2020-07-20 Add hardware design files and edit README
    [encoder-holder.f3d, encoder-holder.stl, encoder-ring.f3d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]
2020-07-21 Complete bill of materials
2020-07-21 Describe 3d prints
    [wheelchair-bracket-2.stl, wheelchair-bracket-3.stl]
2020-07-21 Further documentation of the assembly
2020-07-21 Finish assembly instructions and resize images
2020-07-24 Add driver usage guide

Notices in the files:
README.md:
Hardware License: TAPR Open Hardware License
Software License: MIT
